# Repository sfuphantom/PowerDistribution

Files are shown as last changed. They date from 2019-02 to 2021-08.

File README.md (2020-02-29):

# Power Distributuion Board

Power Distribution Board: Provides protection on the low voltage circuitry

This Board has an input of 12V and provides Output pins for 12V and 5V with a minimum total output current of 10A and a maximum of 35A. All the output pins have Undervoltage/Overvoltage Protection, Reverse Input Protection and Current Surge Protection. PDB uses the following IC's:

- [LT4363](https://www.digikey.ca/products/en?keywords=LT4363CMS-2%23PBF)
- [AP65550FN-7](https://www.digikey.ca/product-detail/en/diodes-incorporated/AP65550FN-7/AP65550FN-7DICT-ND/5147405)

## Library Correlation

Name | Sch Lib | Footprint Lib
---|---|---
Inductor|1264EY-3R3N=P3|IND-6mm
LED green| 150060VS75000 |LED
2 pin header|0768250002|MOLEX_2_pin_MEGAFIT
5V buck|AP65550FN-7|DFN-10
10pF|C0805C100K5RAC7800|CAPC1613X09N
0.1uF/100nF|CL10A104KA8NNNC|CAPC1613X09N
1uF|CL21B105KBFVPNE|CAPC1613X09N
22uF|CL31B226KPHNNNE|CAPC1613X09N
100k|ERA-6AEB104V|R0805
124k|ERA-6AEB1243V|R0805
47nF|GCM188R71H473KA55D|CAPC1613X09N
10uF|GRM21BR71A106KA73L|CAPC1613X09N
N-channel mosfet|IRLR2908TRLPBF|DPAK
LT4363|LT4363CMS-2#PBF|TSOP65P490X110-12N
10mOhm|PE2512FKE7W0R01L|R2512
5k|PNM0805E5001BST5|R0805
Red LED|QTLP600CRTR|LED
2.2k|RC0805FR-072K2L|R0805
10Ohm|RL1220S-100-F|R0805
42.2k|RMCF1210FT42R2|R0805
1k|RNCF0805DTE1K00|R0805
10k|RNCF0805DTE10K0|R0805
20k|RNCF0805DTE20K0|R0805
22.1k|RNCF0805DTE22K1|R0805
TVS diode|SMAJ58A-13-F|DIODE_TVS
32 Pin Molex Connector|05595932|MOLEX_32PIN
|||

## PDB will supply voltages to the following components

|Sr. No.|Board name|Voltage provided|Current Rating|
|---|---|---|---|
|1|VCU|12V|1A|
|2|BMS Master|12V|1A|
|3|BMS slave|Not provided by PDB|-|
|4|Thermistor Expansion|3.3V (Not provided bt PDB)|-|
|5|BSPD|5V|1A|
|6|TSAL|12V|3A|
|7|Shutdown|5V|2A|
|7|Charging shutdown|5V|1A|
|7|Precharge/Discharge|5V|1A|
|8|Brake Lights|12V|1A|
|9|Dashboard|5V and 12V|1A and 1A|
|10|APPS|5V|1A|
|11|BSE|5V|1A|
|12|HV|5V|1A|
|13|Brake Light|12V|3A|
||||
|Total|5V|8|9A|
|Total|12V|6|10A|
||||

Here's a look at the most recent version of the Board:

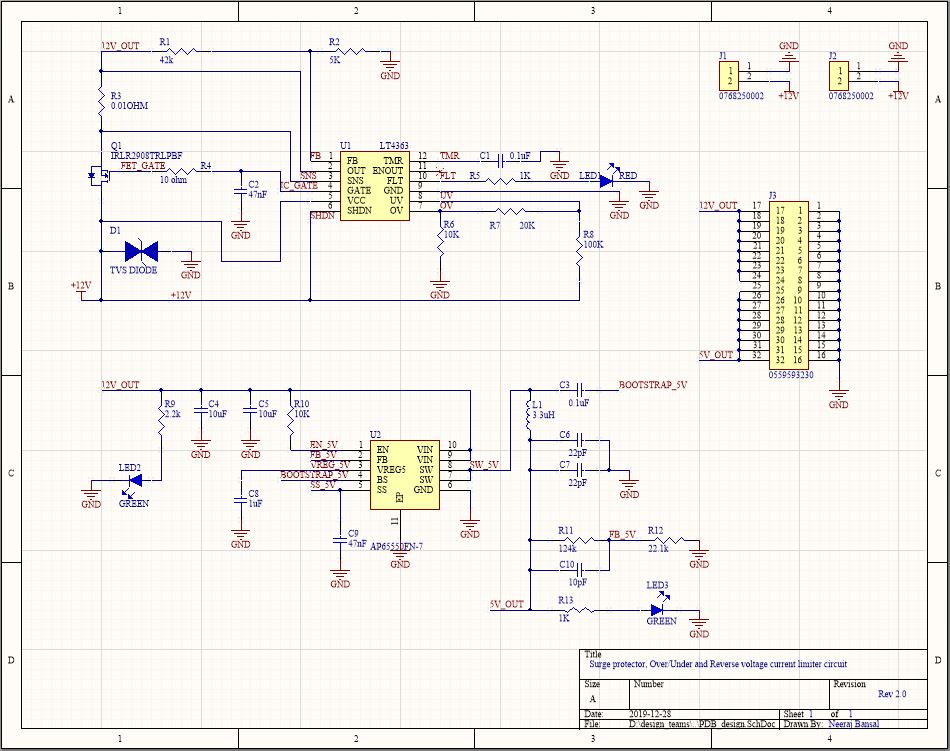
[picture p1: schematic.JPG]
schematic

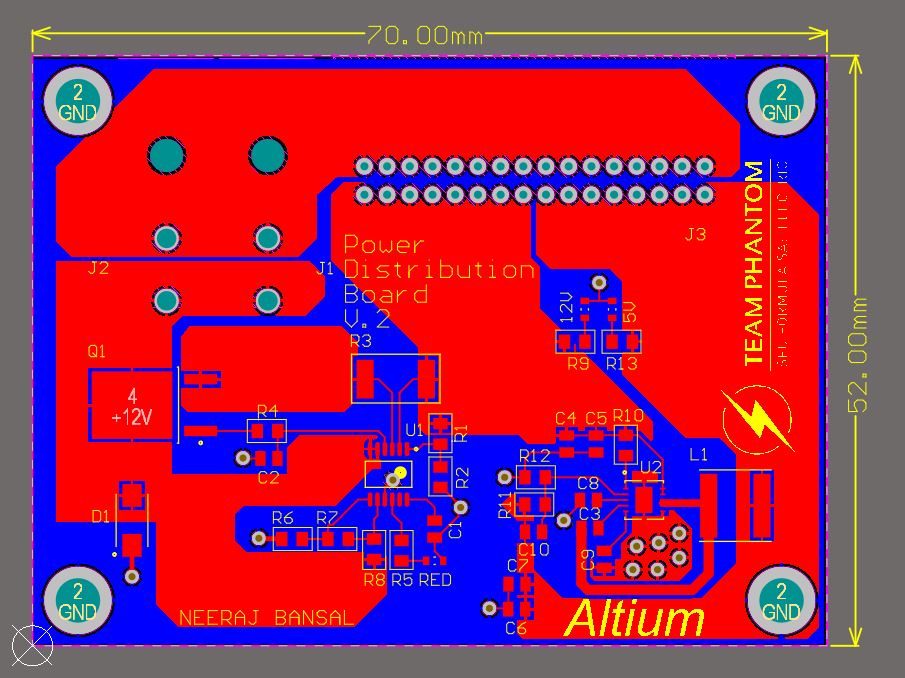
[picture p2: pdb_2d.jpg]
2D PDB

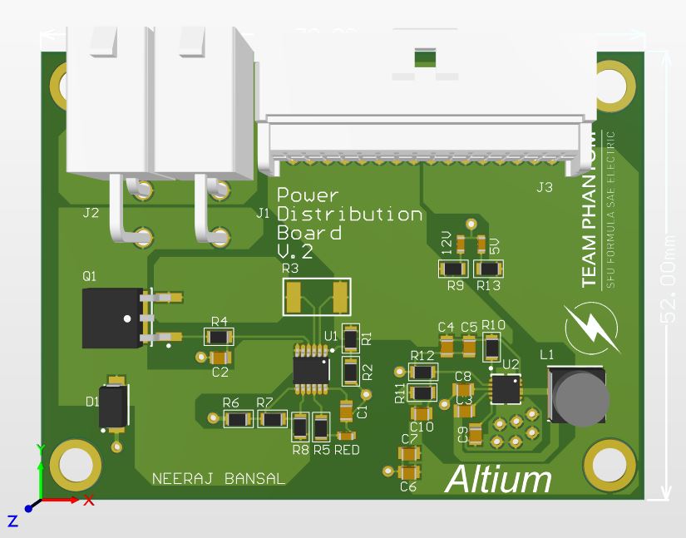
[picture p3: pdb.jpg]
PDB


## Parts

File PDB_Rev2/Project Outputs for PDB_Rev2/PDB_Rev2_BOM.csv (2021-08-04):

Quantity | Description | Designator | Manufacturer 1 | Manufacturer Part Number 1 | Supplier 1 | Supplier Part Number 1
1 | CAP CER 0.047UF 50V X7R 0603 | C1 | Yageo | CC0603KRX7R9BB473 | Digi-Key | 311-1427-6-ND
2 | CAP CER 0.1UF 50V Y5V 0805 | C2, C8 | KEMET | C0805C104Z5VACTU | Digi-Key | 399-1177-6-ND
1 | CAP CER 0.1UF 16V X7R 0603 | C3 | KEMET | C0603C104M4RACTU | Digi-Key | 399-1099-6-ND
1 | CAP CER 0.1UF 16V Y5V 0805 | C4 | KEMET | C0805C104Z4VACTU | Digi-Key | 399-9159-6-ND
1 | 0603 100 pF 50 V ±5% Tolerance C0G/NP0 SMT Multilayer Ceramic Capacitor | C5 | Kyocera AVX | 06035A101JAT2A/4K | Digi-Key | 478-1175-6-ND
1 | KEMET T591D107M010ATE080 Surface Mount Tantalum Capacitor, AEC-Q200 T591 Series, 100uF, 2917 [7343-31 Metric], 0.08 ohm | C6 | KEMET | T591D107M010ATE080 | Digi-Key | 399-12364-1-ND
1 | Aluminum Electrolytic Capacitors - SMD 22uF 50 Volts 20% LYTICS/IC | C7 | CDE Illinois Capacitor | 226SML050M | Digi-Key | 1572-1392-6-ND
1 | TVS DIODE 58VWM 93.6VC SMA | D1 | Diodes | SMAJ58A-13-F | Digi-Key | SMAJ58A-13-FDIDKR-ND
1 | LED RED CLEAR 0603 SMD | D2 | Wurth Electronics | 150060RS75000 | Digi-Key | 732-4978-6-ND
1 | DIODE SCHOTTKY 40V 8A DO214AB | D3 | MCC | SK84L-TP | Digi-Key | SK84L-TPMSDKR-ND
2 | LED GREEN CLEAR 0603 SMD | D4, D5 | Wurth Electronics | 150060VS75000 | Digi-Key | 732-4980-1-ND
2 | CONN HEADER R/A 2POS | J1, J2 | Molex | 76825-0002 | Digi-Key | WM11969-ND
1 | CONN HEADER R/A 4POS 3.5MM | J3 | Molex | 172316-1104 | Digi-Key | WM11594-ND
2 | Single layer pad TP | JP1, JP2
1 | Inductor Power Shielded Wirewound 10uH 10% 100KHz Ferrite 30A 0.0016Ohm DCR Automotive Tray | L1 | Bourns | PQ2614BLA-100K | Digi-Key | PQ2614BLA-100K-ND
1 | Trans MOSFET N-CH 250V 33A 3-Pin(2+Tab) D2PAK T/R | Q1 | Rochester Electronics | FDB33N25TM | Digi-Key | FDB33N25TMDKR-ND
1 | MOSFET P-CH 30V 27A TO252 | Q2 | Diodes | DMP3028LK3-13 | Digi-Key | DMP3028LK3-13DICT-ND
1 | BOURNS - CSS2H-2512K-2L00F - SMD Current Sense Resistor, 0.002 ohm, CSS2H-2512 Series, 2512 [6432 Metric], 5 W, ± 1% | R1 | Bourns | CSS2H-2512K-2L00F | Digi-Key | CSS2H-2512K-2L00FDKR-ND
1 | RES SMD 10 OHM 1% 1/10W 0603 | R2 | Yageo | AC0603FR-0710RL | Digi-Key | 311-10LDDKR-ND
1 | RES SMD 665 OHM 1% 1/10W 0603 | R3 | Yageo | RC0603FR-07665RL | Digi-Key | 311-665HRDKR-ND
1 | RES SMD 47.5K OHM 1% 1/10W 0603 | R4 | Yageo | RC0603FR-0747K5L | Digi-Key | 311-47.5KHRCT-ND
1 | RES SMD 8.06K OHM 1% 1/10W 0603 | R5 | Panasonic | ERJ-3EKF8061V | Digi-Key | P8.06KHDKR-ND
1 | RES SMD 5.1K OHM 1% 1/8W 0805 | R6 | TE Connectivity Holsworthy | CRG0805F5K1 | Digi-Key | A126379DKR-ND
1 | RES 117K OHM 0.5% 1/10W 0603 | R7 | Yageo | RT0603DRE07117KL | Digi-Key | 13-RT0603DRE07117KLDKR-ND
1 | RES 10K OHM 1% 1/10W 0603 | R8 | Yageo | RC0603FR-1010KL | Digi-Key | 13-RC0603FR-1010KLCT-ND
1 | Res Thin Film 0603 3.4K Ohm 0.1% 1/10W ±25ppm/°C Molded SMD Paper T/R | R10 | TE Connectivity | RP73PF1J3K4BTDF | Digi-Key | A110159DKR-ND
2 | RES SMD 2.2K OHM 1% 1/10W 0603 | R11, R12 | Yageo Phycomp | RC0603FR-072K2L | Digi-Key | 311-2.20KHRDKR-ND
1 | RES SMD 10K OHM 5% 1/10W 0603 | R13 | Yageo | RC0603JR-0710KL | Digi-Key | 311-10KGRDKR-ND
1 | RES SMD 6.65K OHM 0.1% 1/6W 0603 | R14 | TE Connectivity | RP73PF1J6K65BTDF | Digi-Key | A110187DKR-ND
1 | Res Thick Film 0603 24K Ohm 1% 0.1W(1/10W) ±100ppm/C Molded SMD Automotive Paper T/R | R15 | Vishay | CRCW060324K0FKEA | Digi-Key | 541-24.0KHCT-ND
1 | RES SMD 665 OHM 1% 1/10W 0603 | R16 | Yageo | RC0603FR-07665RL | Digi-Key | 311-665HRDKR-ND
1 | RES SMD 180 OHM 1% 1/10W 0603 | R17 | TE Connectivity | CRGCQ0603F180R | Digi-Key | A129679DKR-ND
1 | RES SMD 7.87K OHM 1% 1/10W 0603 | R18 | Vishay | CRCW06037K87FKEA | Digi-Key | 541-7.87KHCT-ND
1 | IC SURGE STOPPER HV 12-MSOP | U1 | Analog Devices / Linear Technology | LT4363IMS-2#TRPBF | Digi-Key | LT4363IMS-2#TRPBFDKR-ND
1 | Bi Directional Current and Power Monitor 10-Pin VSSOP T/R | U2 | Texas Instruments | INA226AIDGSR | Digi-Key | 296-29034-1-ND
1 | DC DC Cntrlr Single-OUT Buck 4.5V to 35V Input 8-Pin VSSOP T/R | U3 | TI National Semiconductor | LM3489MMX/NOPB | Digi-Key | 296-35277-6-ND
2 | Connector Header Through Hole 20 position 0.100 (2.54mm)" | X1, X2 | Molex | 0702462001 | Digi-Key | WM6548-ND

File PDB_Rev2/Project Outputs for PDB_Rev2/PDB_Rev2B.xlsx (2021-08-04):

Quantity | Designator | Description | Manufacturer | Manufacturer Part Number
1 | C5 | 0603 100 pF 50 V ±5% Tolerance C0G/NP0 SMT Multilayer Ceramic Capacitor | Kyocera AVX | 06035A101JAT2A\4K
1 | C7 | Aluminum Electrolytic Capacitors - SMD 22uF 50 Volts 20% LYTICS/IC | CDE Illinois Capacitor | 226SML050M
1 | U2 | Bi Directional Current and Power Monitor 10-Pin VSSOP T/R | Texas Instruments | INA226AIDGSR
1 | R1 | BOURNS - CSS2H-2512K-2L00F - SMD Current Sense Resistor, 0.002 ohm, CSS2H-2512 Series, 2512 [6432 Metric], 5 W, ± 1% | Bourns | CSS2H-2512K-2L00F
1 | C1 | CAP CER 0.047UF 50V X7R 0603 | Yageo | CC0603KRX7R9BB473
1 | C3 | CAP CER 0.1UF 16V X7R 0603 | KEMET | C0603C104M4RACTU
1 | C4 | CAP CER 0.1UF 16V Y5V 0805 | KEMET | C0805C104Z4VACTU
2 | C2, C8 | CAP CER 0.1UF 50V Y5V 0805 | KEMET | C0805C104Z5VACTU
2 | J1, J2 | CONN HEADER R/A 2POS | Molex | 76825-0002
1 | J3 | CONN HEADER R/A 4POS 3.5MM | Molex | 172316-1104
2 | X1, X2 | Connector Header Through Hole 20 position 0.100" (2.54mm)
1 | U3 | DC DC Cntrlr Single-OUT Buck 4.5V to 35V Input 8-Pin VSSOP T/R | TI National Semiconductor | LM3489MMX/NOPB
1 | D3 | DIODE SCHOTTKY 40V 8A DO214AB | MCC | SK84L-TP
1 | U1 | IC SURGE STOPPER HV 12-MSOP | Analog Devices / Linear Technology | LT4363IMS-2#TRPBF
1 | L1 | Inductor Power Shielded Wirewound 10uH 10% 100KHz Ferrite 30A 0.0016Ohm DCR Automotive Tray | Bourns | PQ2614BLA-100K
1 | C6 | KEMET T591D107M010ATE080 Surface Mount Tantalum Capacitor, AEC-Q200 T591 Series, 100uF, 2917 [7343-31 Metric], 0.08 ohm | KEMET | T591D107M010ATE080
2 | D4, D5 | LED GREEN CLEAR 0603 SMD | Wurth Electronics | 150060VS75000
1 | D2 | LED RED CLEAR 0603 SMD | Wurth Electronics | 150060RS75000
1 | Q2 | MOSFET P-CH 30V 27A TO252 | Diodes | DMP3028LK3-13
1 | R8 | RES 10K OHM 1% 1/10W 0603 | Yageo | RC0805FR-0710KL
1 | R7 | RES 117K OHM 0.5% 1/10W 0603 | Yageo | RT0603DRE07117KL
2 | R11, R12 | RES SMD 2.2K OHM 1% 1/10W 0603 | Yageo Phycomp | RC0603FR-072K2L
1 | R6 | RES SMD 5.1K OHM 1% 1/8W 0805 | TE Connectivity | 1623257-1
1 | R14 | RES SMD 6.65K OHM 0.1% 1/6W 0603 | TE Connectivity | 8-2176088-4
1 | R18 | RES SMD 7.87K OHM 1% 1/10W 0603 | Vishay | CRCW06037K87FKEA
1 | R5 | RES SMD 8.06K OHM 1% 1/10W 0603 | Panasonic | ERJ-3EKF8061V
1 | R2 | RES SMD 10 OHM 1% 1/10W 0603 | Yageo | RC0805FR-0710RL
1 | R13 | RES SMD 10K OHM 5% 1/10W 0603 | Yageo | RC0603JR-0710KL
1 | R4 | RES SMD 47.5K OHM 1% 1/10W 0603 | Vishay | CRCW080547K5FKEA
1 | R17 | RES SMD 180 OHM 1% 1/10W 0603 | TE Connectivity | CRGCQ0603F180R
2 | R3, R16 | RES SMD 665 OHM 1% 1/10W 0603 | Yageo | RC0603FR-07665RL
1 | R15 | Res Thick Film 0603 24K Ohm 1% 0.1W(1/10W) ±100ppm/C Molded SMD Automotive Paper T/R | Vishay | CRCW060324K0FKEA
1 | R10 | Res Thin Film 0603 3.4K Ohm 0.1% 1/10W ±25ppm/°C Molded SMD Paper T/R | TE Connectivity | RP73PF1J3K4BTDF
2 | JP1, JP2 | Single layer pad TP
1 | Q1 | Trans MOSFET N-CH 250V 33A 3-Pin(2+Tab) D2PAK T/R | ON Semiconductor / Fairchild | FDB33N25TM
1 | D1 | TVS DIODE 58VWM 93.6VC SMA | Diodes | SMAJ58A-13-F

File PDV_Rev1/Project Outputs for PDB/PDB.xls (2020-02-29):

Comment | Description | Designator | Footprint | LibRef | Quantity
0.1uF | 0.1µF ±10% 25V Ceramic Capacitor X5R 0603 (1608 Metric) | C1, C3 | CAPC1613X09N | CL10A104KA8NNNC | 2
47nF | CAP CER 0.047UF 50V X7R 0603 | C2, C9 | CAPC1613X09N | GCM188R71H473KA55D | 2
10uF | 10µF ±10% 10V Ceramic Capacitor X7R 0805 (2012 Metric) | C4, C5 | CAPC1613X09N | GRM21BR71A106KA73L | 2
22pF | 22µF ±10% 10V Ceramic Capacitor X7R 1206 (3216 Metric) | C6, C7 | CAPC1613X09N | CL31B226KPHNNNE | 2
1uF | 1µF ±10% 50V Ceramic Capacitor X7R 0805 (2012 Metric) | C8 | CAPC1613X09N | CL21B105KBFVPNE | 1
10pF | 10pF ±10% 50V Ceramic Capacitor X7R 0805 (2012 Metric) | C10 | CAPC1613X09N | C0805C100K5RAC7800 | 1
TVS DIODE | TVS DIODE 58VWM 93.6VC SMA | D1 | DIODE_TVS | SMAJ58A-13-F | 1
768250002 | CONN_2Position_MEGAFIT Molex Through Hole, Right Angle Tin | J1, J2 | MOLEX_2PIN_MEGAFIT | 768250002 | 2
559593230 |  | J3 | MOLEX_32PIN | 559593230 | 1
3.3uH | IND 3.3µH 6.5A 25.2 mOhm Max Nonstandard | L1 | IND-6mm | 1264EY-3R3N=P3 | 1
RED | Red LED Indication - Discrete 2V 0603 (1608 Metric) | LED1 | LED | QTLP600CRTR | 1
GREEN | LED GREEN CLEAR 0603 SMD | LED2, LED3 | LED | 150060VS75000 | 2
IRLR2908TRLPBF | MOSFET N-CH 80V 30A DPAK | Q1 | DPAK | IRLR2908TRLPBF | 1
42k | 42k | R1 | R0805 | RNCF0805DTE10K0_2_2 | 1
5K | 5 kOhms ±0.1% 0.2W, 1/5W Chip Resistor 0805 (2012 Metric) Anti-Sulfur, Moisture Resistant, Non-Inductive, Non-Magnetic Thin Film | R2 | R0805 | PNM0805E5001BST5 | 1
0.01OHM | RES SMD 0.01 OHM 1% 2W 2512 | R3 | R2512 | PE2512FKE7W0R01L | 1
10 ohm | RES SMD 10 OHM 1% 1/3W 0805 | R4 | R0805 | RL1220S-100-F | 1
1K | 1 kOhms ±0.5% 0.125W, 1/8W Chip Resistor 0805 (2012 Metric) Automotive AEC-Q200 Thin Film | R5, R13 | R0805 | RNCF0805DTE1K00 | 2
10K | Res Thin Film 0805 10K Ohm 0.5% 0.1W(1/10W) ±25ppm/C Molded SMD Paper T/R | R6, R10 | R0805 | RNCF0805DTE10K0 | 2
20K | 20 kOhms ±0.5% 0.125W, 1/8W Chip Resistor 0805 (2012 Metric) Automotive AEC-Q200 Thin Film | R7 | R0805 | RNCF0805DTE20K0 | 1
100K | Res Thin Film 0805 100K Ohm 0.1% 0.125W(1/8W) ±25ppm/C Molded SMD Automotive Punched T/R | R8 | R0805 | ERA-6AEB104V | 1
2.2k | 2.2 kOhms ±1% 0.125W, 1/8W Chip Resistor 0805 (2012 Metric) Moisture Resistant Thick Film | R9 | R0805 | RC0805FR-072K2L | 1
124k | 124 kOhms ±0.1% 0.125W, 1/8W Chip Resistor 0805 (2012 Metric) Automotive AEC-Q200 Thin Film | R11 | R0805 | ERA-6AEB1243V | 1
22.1k | 22.1 kOhms ±0.5% 0.125W, 1/8W Chip Resistor 0805 (2012 Metric) Automotive AEC-Q200 Thin Film | R12 | R0805 | RNCF0805DTE22K1 | 1
LT4363 | IC SURGE STOPPER HV 12-MSOP | U1 | TSOP65P490X110-12N | LT4363CMS-2#PBF | 1
AP65550FN-7 | IC BUCK SYNC 5A, 18V VIN MAX 650kHz COT Step-Down Conv | U2 | DFN-10 | AP65550FN-7 | 1

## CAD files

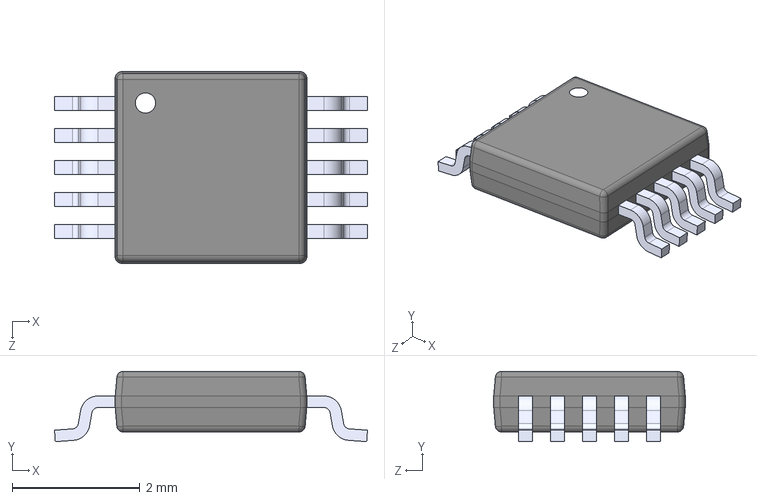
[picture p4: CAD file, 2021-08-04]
PDB_Rev2/PDB Altium footprints/INA226AIDGSR.STEP
4.90 x 1.10 x 3.00 mm

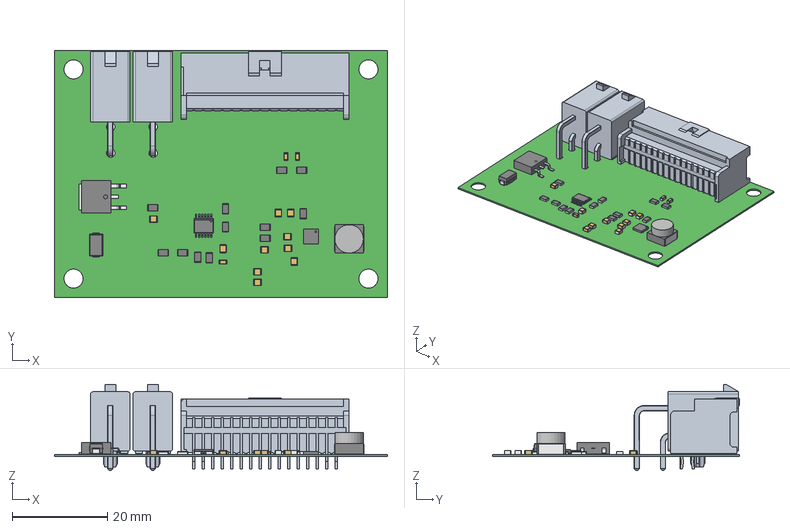
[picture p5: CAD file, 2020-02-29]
PDV_Rev1/PDB_board.step
70.0 x 52.0 x 18.1 mm
Open_CASCADE_STEP_translator_6.8_21.1
Open_CASCADE_STEP_translator_6.8_21.2.1
Thermal_Shape
Open_CASCADE_STEP_translator_6.8_21.4.1 x 10
Open_CASCADE_STEP_translator_6.8_26.1
Open_CASCADE_STEP_translator_6.8_26.2.1
Leader x 12
Mid_Body x 12
Open_CASCADE_STEP_translator_6.8_16.2.1 x 24
Mark x 12
Open_CASCADE_STEP_translator_6.8_10.1
Open_CASCADE_STEP_translator_6.8_10.2.1
Lead x 4
Trimmed_Lead
tab
Open_CASCADE_STEP_translator_6.8_1.1.1 x 3
Open_CASCADE_STEP_translator_6.8_1.1.2 x 3
Open_CASCADE_STEP_translator_6.8_1.2.1 x 3
Open_CASCADE_STEP_translator_6.8_35.3.1 x 2
Open_CASCADE_STEP_translator_6.8_2.1.1
Open_CASCADE_STEP_translator_6.8_20.1.1 x 10
Open_CASCADE_STEP_translator_6.8_20.1.2 x 10
Open_CASCADE_STEP_translator_6.8_20.2.1 x 10

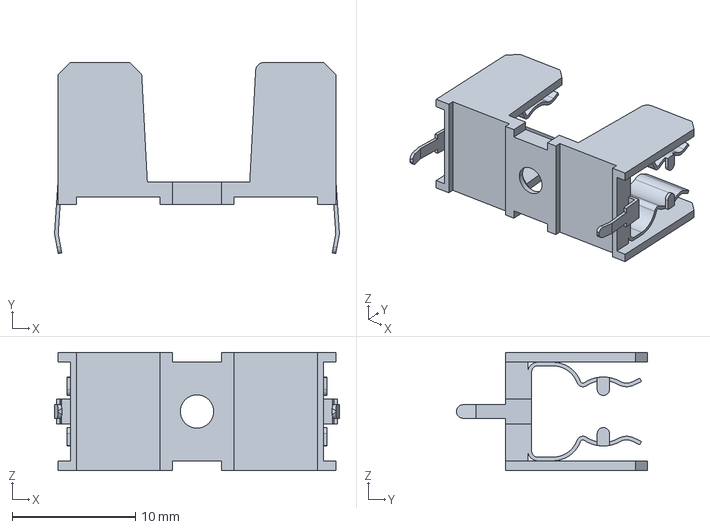
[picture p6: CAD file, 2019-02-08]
PDV_Rev1/step_files/fuse.stp
23.1 x 15.5 x 9.60 mm

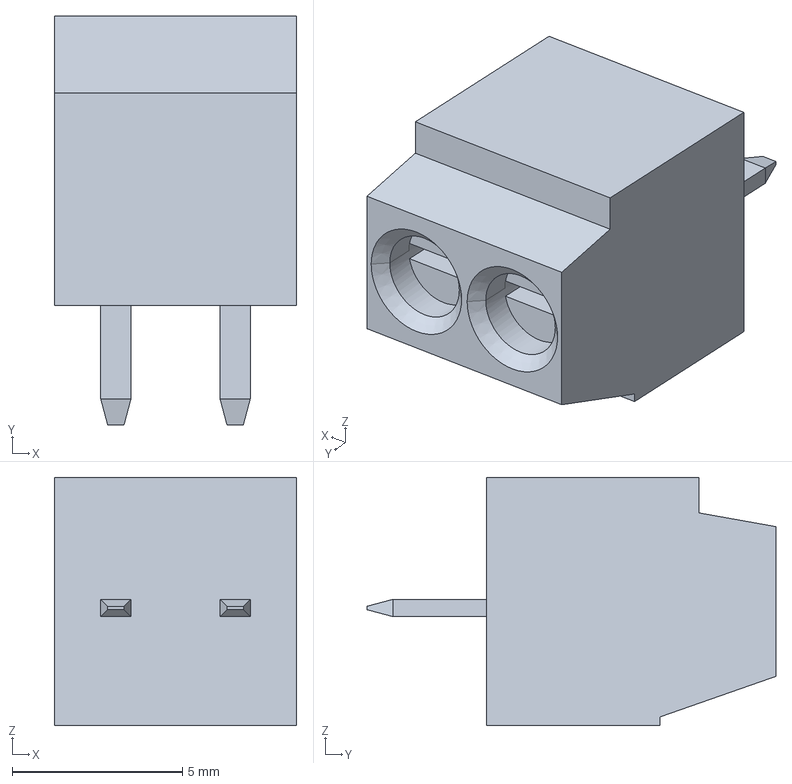
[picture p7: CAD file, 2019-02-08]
PDV_Rev1/step_files/hdr1.stp
7.11 x 12.0 x 7.29 mm

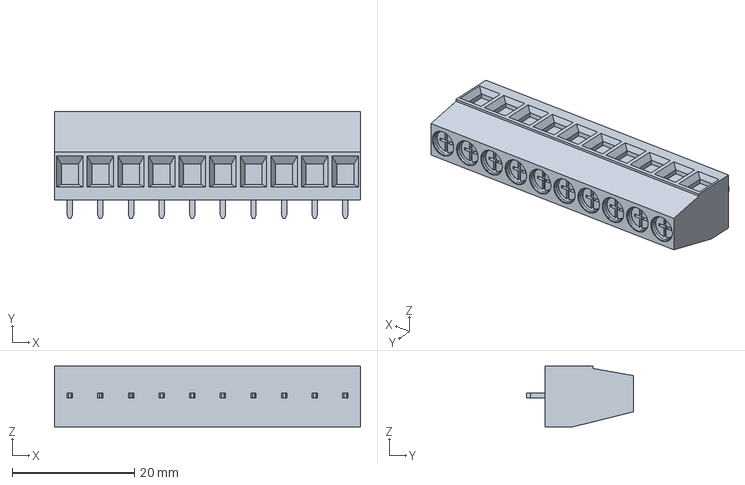
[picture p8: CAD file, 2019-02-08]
PDV_Rev1/step_files/hdr2.stp
50.0 x 17.5 x 9.91 mm

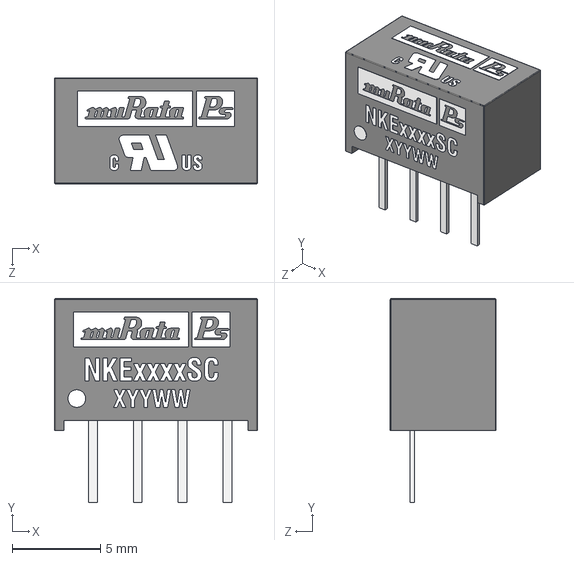
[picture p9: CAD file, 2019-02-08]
PDV_Rev1/step_files/dcdc2.step
11.5 x 11.6 x 6.02 mm

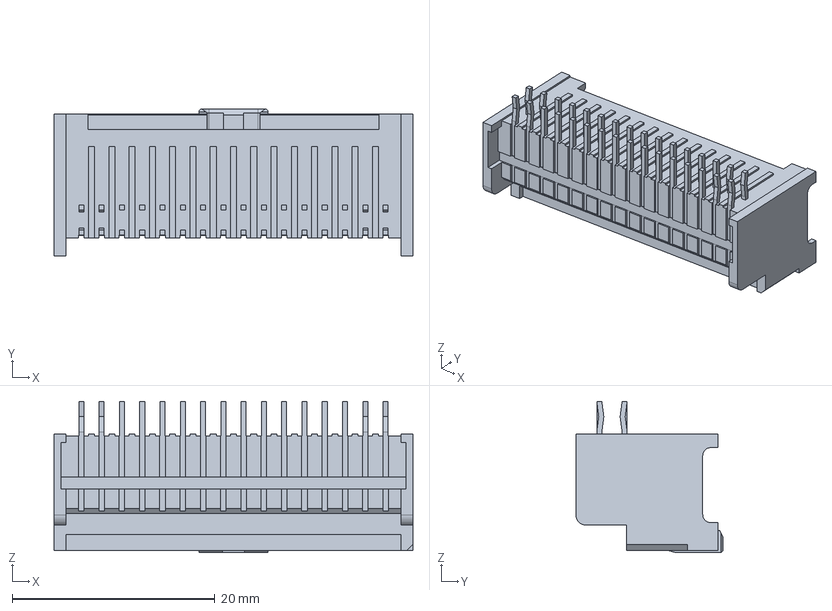
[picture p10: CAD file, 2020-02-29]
PDV_Rev1/step_files/559593230.stp
35.4 x 14.5 x 14.9 mm

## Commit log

2019-02-08 Bringing in all of old PDB design files
    [NEW_PDB.SchDoc, PCB.REV6.PcbDoc, PDB.PcbDoc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]
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2019-05-25 Finished the PCB for PDB, please add input connectors and clean up the schematic. Thanks
    [3dparts.pcblib, NEW_PDB.SchDoc, PDB.PrjPCB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]
2019-05-26 added power input connector. 1 Voilation and then ready for gbr
    [NEW_PDB.SchDoc, PDB.PrjPCB, PDB_final_han.PcbDoc]
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2019-06-03 cleaned up schematic and little PCB fixes
    [NEW_PDB.SchDoc, PDB_final_han.PcbDoc, symbols.SchLib]
2019-06-06 added mount holes and LED's for fault and power
    [NEW_PDB.SchDoc, PDB_final_han.PcbDoc]
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2019-06-17 small fixes
    [NEW_PDB.SchDoc, PDB_final_han.PcbDoc]
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2019-08-17 added fuses and corrected Rsns tracks
    [NEW_PDB.SchDoc, PDB.PrjPCB, PDB_Components.PcbLib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]
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2019-08-25 changed connector with more outputs and completed board
    [NEW_PDB.SchDoc, PDB_Components.PcbLib, PDB_components.SchLib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]
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2019-11-16 fixed the lt4363 circuitry and changed the PCB layout
    [NEW_PDB.SchDoc, PDB_neeraj.PcbDoc]
2019-11-24 PDB updated, output not generated and BOM needs update
    [NEW_PDB.SchDoc, PDB.PrjPCB, PDB_neeraj.PcbDoc]
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2019-12-26 design completion, needs minor changes like verifying, orientation etc
    [PDB.PcbDoc, PDB.PcbLib, PDB.SchDoc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]
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2019-12-28 final edits and gerber, step and BOM generated
    [PDB.PrjPCB, PDB.xls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]
2020-01-01 silkscreen fixes
    [PDB_board.PcbDoc]
2020-02-01 minor fixes, and silkscreen
    [PDB_board.PcbDoc, PDB_design.SchDoc]
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2020-02-04 fixed power header holes, regenerated gerbers
    [PDB_Components.PcbLib, PDB_board.PcbDoc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]
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2021-02-22 Addition of 2 missing libraries
    [U3_U4.SchDoc]
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2021-02-25 Addition of IC U4, 12V to 5V buck converter to IC lib and Schematic
    [PCB_Project1.PrjPCB, U3_U4.SchDoc]
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2021-02-26 Project fix from 2 to 1 project on altium
    [PCB_Project1.PrjPCB, PDB_Rev2.PrjPcb, U3_U4.SchDoc]
2021-02-26 Minor fixes
    [PCB_Project1.PrjPCB, PDB_Rev2.PrjPcb]
2021-02-28 Added components to the schematic library and added respective components to the IC1 Schematic.
    [PDB_Rev2.PrjPcb, Schlib1.SchLib, U1 Schematic.SchDoc]
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2021-03-02 Finished editing the IC1 schematic, and also added in two 2x1 pin connectors
    [Schlib1.SchLib, U1 Schematic.SchDoc]
2021-03-04 integration of ICs, shortlisting connectors
    [U1 Schematic.SchDoc, U3_U4.SchDoc]
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2021-03-06 Updated U1 by making it readable like a book where the input voltage enters from the left and the output voltage leaves from the right
    [Schlib1.SchLib, U1 Schematic.SchDoc]
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2021-03-06 Changes to the schematic look of U2 to make it left to right, fixed connecotrs, connection fixes to U3
    [PDB_Rev2.PrjPcb, U1 Schematic.SchDoc, U3_U4.SchDoc]
2021-03-07 In IC1 changed C1 from 47nF to 100nF (aka 0.1uF)
    [U1 Schematic.SchDoc]
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2021-03-10 Schematic review 2A, schematic 1 edits, minor changes to schematic 2
    [PDB_Rev2.PrjPcb, U1 Schematic.SchDoc, U3_U4.SchDoc]
2021-03-10 Removed the LED from FLT pin and placed two LEDs by the input and output
    [U1 Schematic.SchDoc]
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2021-03-11 sch. review 2-B end, only U3 inductor selection is left
    [Output.SchDoc, PDB_Rev2.PrjPcb, Protection.SchDoc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]
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2021-03-15 Removed Neeraj's Files, cleaned up branch, changed names of .SchDoc files
    [559593230.stp, Output.SchDoc, PDB.PrjPCB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]
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2021-03-17 added new output cap and fixed R1
    [PDB_Protection.SchDoc, PDB_Supply.SchDoc]
2021-03-17 Post meeting discussion, addition of a diode footprint
    [PDB_PCB_lib.PcbLib, PDB_Rev2_PCB.PcbDoc, PDB_Supply.SchDoc]
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2021-03-20 Added some more footprints, only 20 pin connector left
    [PDB_PCB_lib.PcbLib, PDB_Supply.SchDoc]
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2021-03-20 forgot to update schematics with some footprints, still only inductor left
    [PDB_Supply.SchDoc]
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2021-03-20 added all components to PCB doc, new PCB doc, deleted the old PCB doc
    [PDB_PCB_lib.PcbLib, PDB_Protection.SchDoc, PDB_Rev2.PcbDoc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]
2021-03-21 component placement for 2nd schematic in PCB doc
    [PDB_Rev2.PcbDoc, PDB_Supply.SchDoc]
2021-03-21 Laid out the components of the U1 schematic in the PCB file and detangled the mess
    [PDB_Protection.SchDoc, PDB_Rev2.PcbDoc]
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2021-03-28 Updated the dimensions and placement of components of the PCB
    [PDB_Rev2.PcbDoc]
2021-03-29 minor changes in the cancelled PCB review, actual review tomorrow
    [PDB_Rev2.PcbDoc, PDB_Supply.SchDoc]
2021-03-31 Changed the 0805 resistors to 0603 for visual appeal, also added a Route schematic
    [PDB_Protection.SchDoc, PDB_Rev2.PcbDoc, PDB_Rev2.PrjPcb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]
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2021-04-12 Added a polygon pour and traces to the PCB for U1
    [PDB_Rev2.PcbDoc]
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2021-04-12 same thing (design review 1), but another save for some reason
    [PDB_Protection.SchDoc]
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2021-04-24 Post design review, added mech layer, fixed minor bugs
    [PDB_Rev2.PcbDoc, PDB_Rev2.PrjPcb, PDB_Supply.SchDoc]
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2021-04-25 removed the 0402 res and changed that and 1 more to new values, some routing changes
    [PDB_Rev2.PcbDoc, PDB_Supply.SchDoc, PDB_sch_lib.SchLib]
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2021-05-04 removed an extra GND just chilling somewhere on the schematic
    [PDB_Protection.SchDoc]
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2021-06-13 mosfet footprint fixed
    [DPAK228P990X239-4N.PcbLib, PDB_PCB_lib.PcbLib, PDB_Rev2.PcbDoc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]
2021-06-13 added a note for R4 to be 62K
    [PDB_Protection.SchDoc, PDB_Rev2.PrjPcb]
2021-06-13 post discussion w/ Nina about PDB, no major changes
    [PDB_Protection.SchDoc, PDB_Rev2.PcbDoc, PDB_Supply.SchDoc]
2021-06-13 fixed mosfet gate pin via location and some other minor changes
    [PDB_Rev2.PcbDoc]
2021-07-06 Put all files into a folder, made easier for merging
    [559593230.stp, PDB.PrjPCB, PDB.SchLib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]
2021-07-07 Git fixing, and gerber generating
    [PDB_Rev2.GBL, PDB_Rev2.GBO, PDB_Rev2.GBP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]
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2021-08-09 deleted history files, added altium project for HV Board
    [HV Board PCB Library.PcbLib, HV Board Rev3 2022.PrjPCB, HV Board Schematic Library.SchLib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]
2021-08-22 added documents and sch label and footprint for Vicor DCDC converter
    [HV Board 2022.PrjPCB, HV_Board_2022.PcbDoc, HV_Board_PCB_Lib.PcbLib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]
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2021-10-05 updated altium, added 3D part for Cincon dcdc conveter
    [HV_Board_PCB_Lib.PcbLib]
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2021-10-07 Added more components and schematic design for the HV DCDC circuit
    [HV_Board_2022.PcbDoc, HV_Board_PCB_Lib.PcbLib, HV_Board_Rev3.PrjPCB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]
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2021-10-25 worked on adding connectors, fuses and TVS diodes. Some research on the isolated opamp
    [Connectors_and_Protection.SchDoc, HV_Board_Rev3.PrjPCB, HV_Board_Sch_Lib.SchLib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]
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2022-07-06 Added new schematics and updated old ones for V2022
    [3V3_PSU.SchDoc, Connectors_and_Protection.SchDoc, Current_Monitoring.SchDoc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]
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
